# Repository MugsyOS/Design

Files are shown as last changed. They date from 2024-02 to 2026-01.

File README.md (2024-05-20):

# Design
All the parts! CAD, PCB and STL files for all of Mugsy's physical components. 

# Mech Control PCB
### Files:
* ****Schematic:**** mech-control-SCH-v0.2.fsch
* ****Board:**** mech-control-BRD-v0.2.fbrd
- - -

# Cone Mech
### Files:
* **Cone Pulley (2 files):** Print main and top.
* **Cone Support (1 file):** Print two for both left and right supports.
* **Stepper Motor Mount (1 file)**: Print one
* **Panels:** 
  * STLs provided for both top and bottom panels.
  * DXF files provided for those with access to a laser or CNC. We use 3mm cast acrylic which works out great. Other material can be used but must be 3mm. 
* **Idler Mount (1 File):** Print two.
- - -
### Additional Parts:
* **Stepper Motor**
  * Model:14HR05-0504S
  * Step Angle: 0.9deg
  * Single Unit Source: [STEPPERONLINE](https://www.omc-stepperonline.com/round-nema-14-bipolar-0-9deg-7ncm-9-91oz-in-0-5a-8-5v-36x12mm-4-wires-14hr05-0504s)
* **Signal** **Breakout PCB**: PCB files will be uploaded shortly. Single PCBs will also be available on the web store end of March 2024. 
* **Ethernet Socket:** RJ45 Connector, PCB Mount
* **M3 Threaded Inserts:**
  * Size: M3*4.6x5.7mm
* **M3 x 8mm Hex Head Machine Screws**
* **2GT Timing Pulley:** 
  * Type: 2M-AF
  * 20 Teeth
  * 6mm bore size
* **GT2 Toothless  Idler Pulleys (2x):** 3mm bore size
- - -
# Spout Mech
### Files:
* ****Spout Pulley Assembly (2 files):**** Print main and cap.
* ****Spout Pulley Assembly (2 files):**** Print main and cap.
* ****Spout Arm(1 file)****: Print one
- - -
### Additional Parts:
* ****Stepper Motor****
  * Model: 17HS08-1004S |
  * Step Angle: 1.8 deg
  * Single Unit Source: [STEPPERONLINE](https://www.omc-stepperonline.com/nema-17-bipolar-1-8deg-16ncm-22-6oz-in-1a-3-7v-42x42x20mm-4-wires-17hs08-1004s)
* ****M8 x 50mm Threaded Rod****
* ****8mm Shaft Lock Collar:**** 
  * 8mm(ID) * 14mm (OD) * 7mm (Depth)
* ****2GT Timing Pulley:****
  * 40 Teeth 
  * 8mm Bore Size
* ****GT2 Belt:**** 
  * 156mm * 6mm
- - -
# Screen Mount/Stabilizer
### Files:
* ****Screen Support:**** Left Side (single)
* ****Screen Support:**** Right Side (double)
* ****Screen Mount Main****: Print one
- - -
****All STEP/Fusion CAD source files will be uploaded as soon as possible.****

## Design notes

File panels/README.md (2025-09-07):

Vector files for all outer enclosure panels.

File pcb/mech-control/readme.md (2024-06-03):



**Components:**
* Nano Microcontroller
* 2x DRV8825 Stepper Drivers
* 2x10 pin headers for IO bridge
* 12v input
* 12v pass through
* 2x 47uf electrolytic capacitors
* 3x 100nf decoupling capacitors
* RJ45 Jack for connecting cone mech
* TRRS Jack for connecting spout

⠀**IO Bridge:** The IO bridge exposes all of the unused Nano’s pins except for reset and VIN:
* 2x 3V3
* 2x 5V
* 4x GND
* A0
* A1
* A2
* A4 / SDA
* A5 / SCL
* A6
* A7
* D0
* D1
* D12
* D13
* AREF

All of the analog pins can also be used as digital pins as needed.
**Board Files:** The schematic and board files have been uploaded to the design repo here.

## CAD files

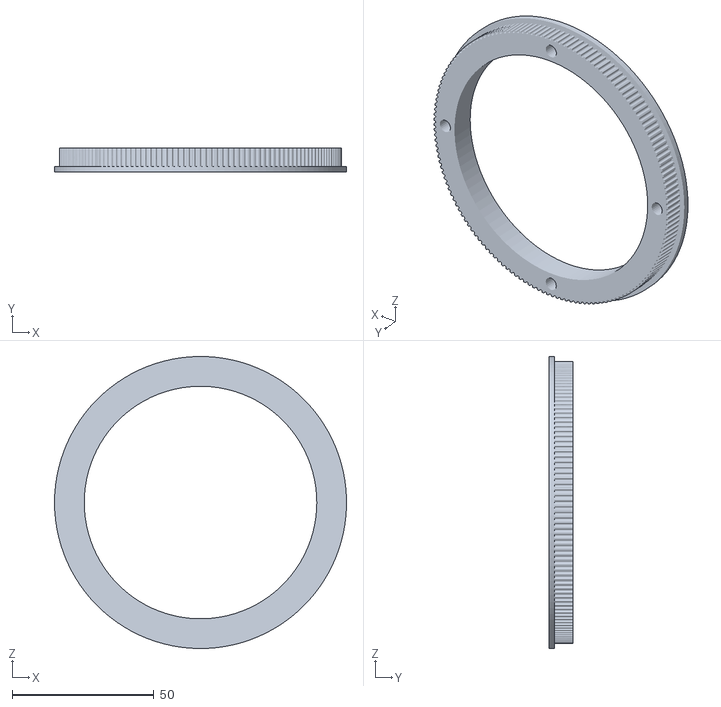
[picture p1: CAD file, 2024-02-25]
cone-mech/cone-pulley/cone-pulley-main-V1.stl
103.0 x 8.50 x 103.0

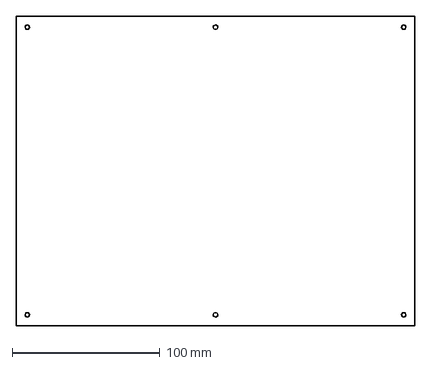
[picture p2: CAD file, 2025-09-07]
panels/head-unit-side-panel-main.dxf
270.0 x 210.0 mm

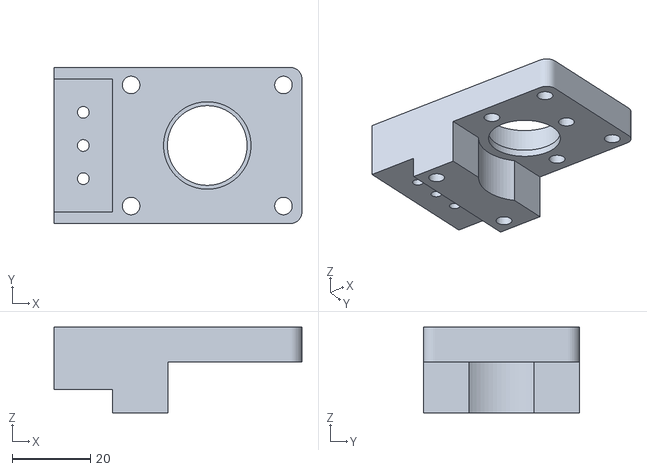
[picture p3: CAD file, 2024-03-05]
spout-mech/mugsy-spout-pulley-main-V0.8.stl
63.5 x 40.0 x 22.0

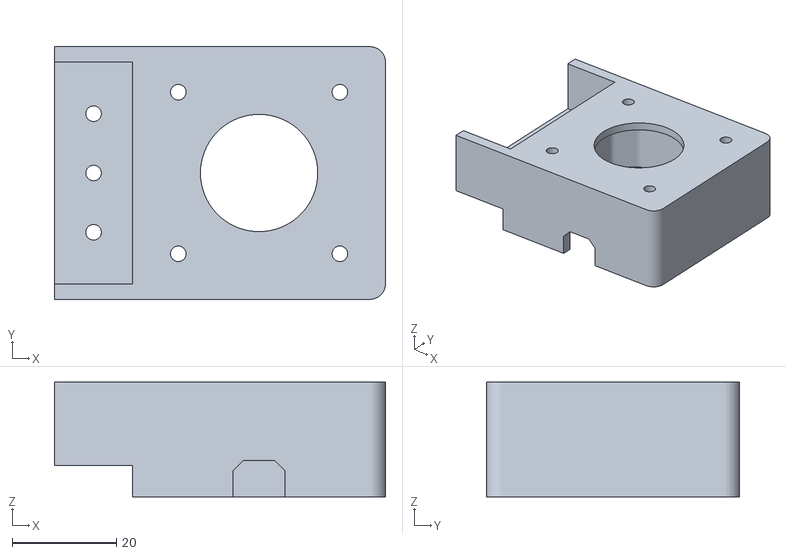
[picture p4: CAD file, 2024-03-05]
spout-mech/mugsy-spout-stepper-main-V0.8.stl
63.5 x 48.5 x 22.0

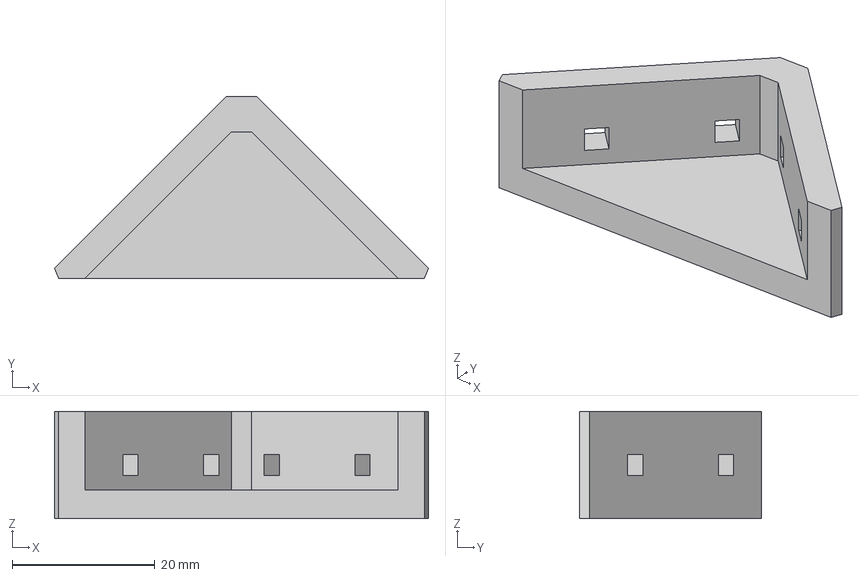
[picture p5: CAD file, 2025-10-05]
brackets/flipped-bracket.3mf
52.3 x 25.5 x 15.0 mm

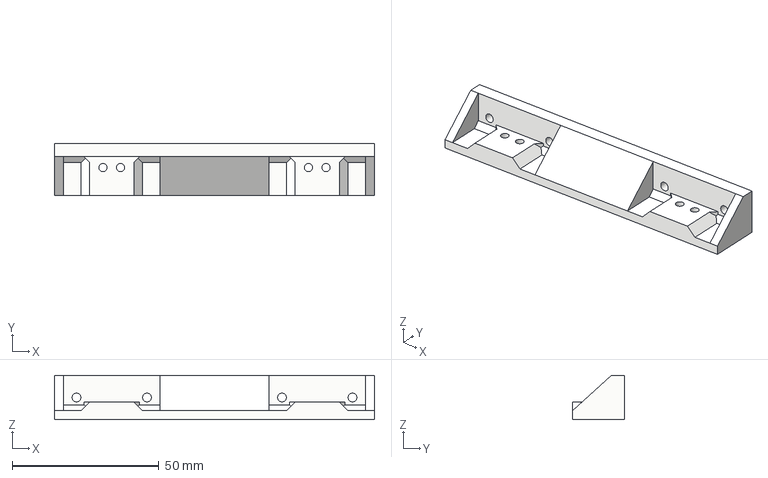
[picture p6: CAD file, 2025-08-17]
cone-mech-platform-scale/extended-mount-wip.3mf
109.0 x 17.7 x 15.0 mm

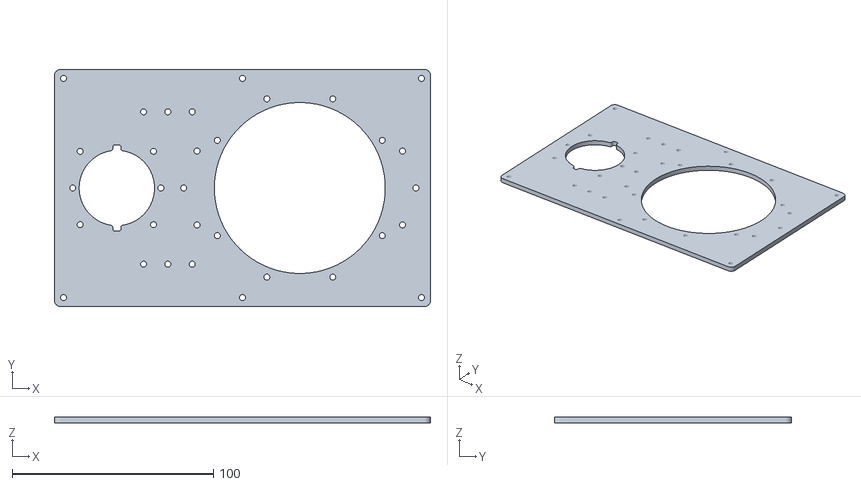
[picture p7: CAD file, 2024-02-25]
cone-mech/bottom-panel-V0.8.stl
187.0 x 118.0 x 3.00

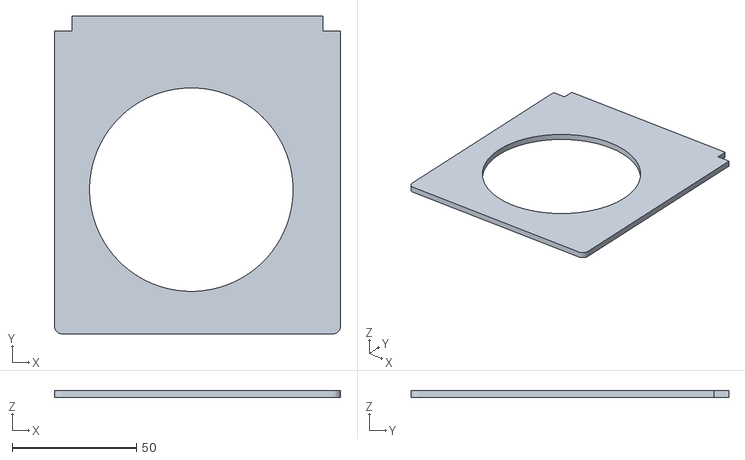
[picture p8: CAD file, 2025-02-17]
grinder/grinder-top-panel.stl
115.3 x 128.1 x 3.00

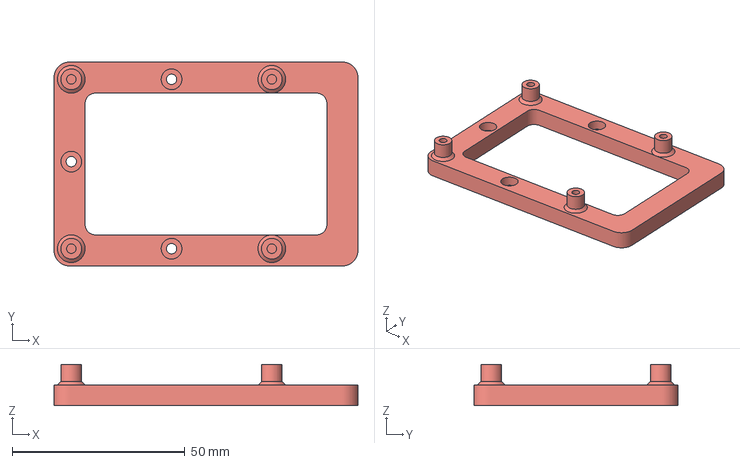
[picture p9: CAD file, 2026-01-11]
pcb/pi-pcb-mount-1 v1.3mf
87.9 x 59.0 x 12.0 mm

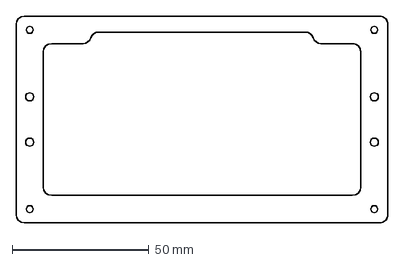
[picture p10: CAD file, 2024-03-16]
screen-mount/stabilizer-mount-V1.dxf
136.2 x 75.7 mm

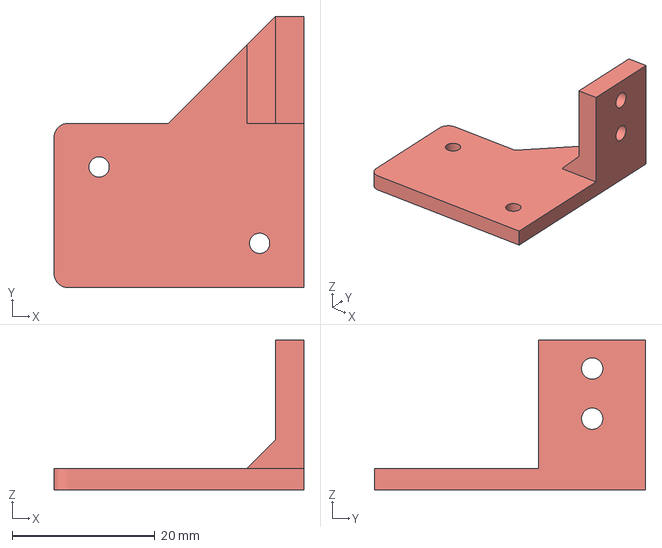
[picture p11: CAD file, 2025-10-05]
spout-mech/limit-mount-reversed.3mf
35.1 x 38.1 x 21.0 mm

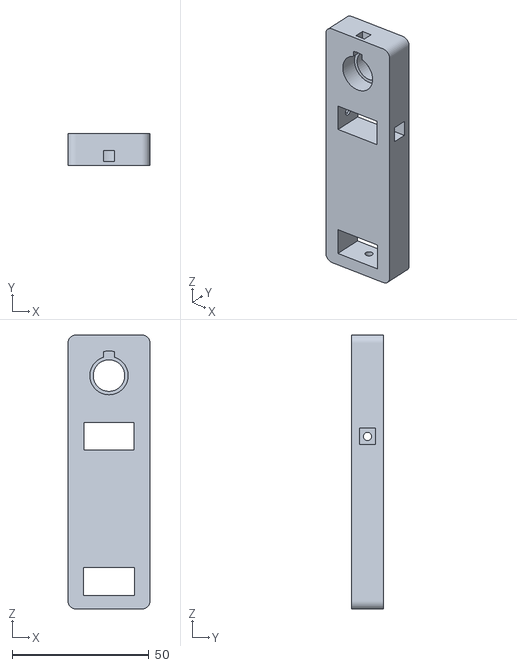
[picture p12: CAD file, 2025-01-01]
spout-mech/spout-v2/spout-arm.stl
30.0 x 11.8 x 100.0

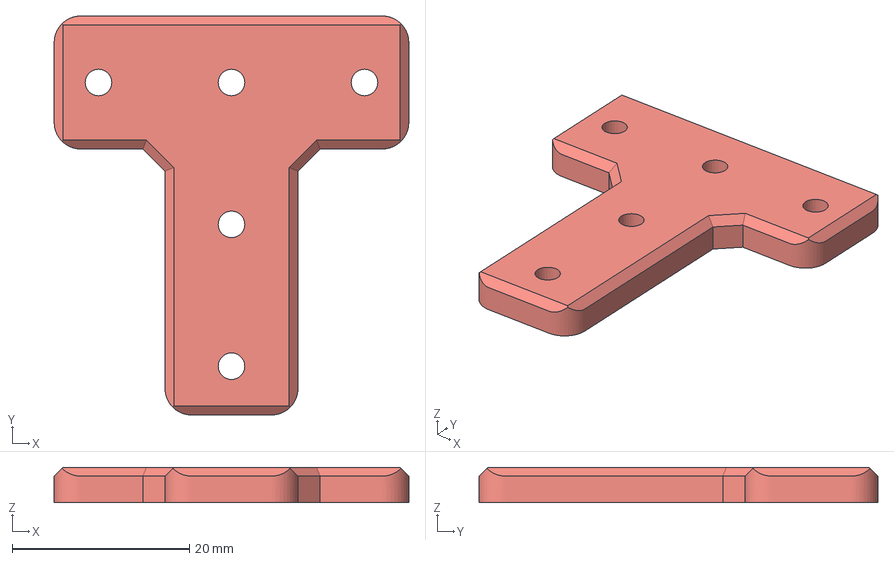
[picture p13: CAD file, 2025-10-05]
brackets/t-shape-bracket.3mf
40.0 x 45.0 x 4.00 mm

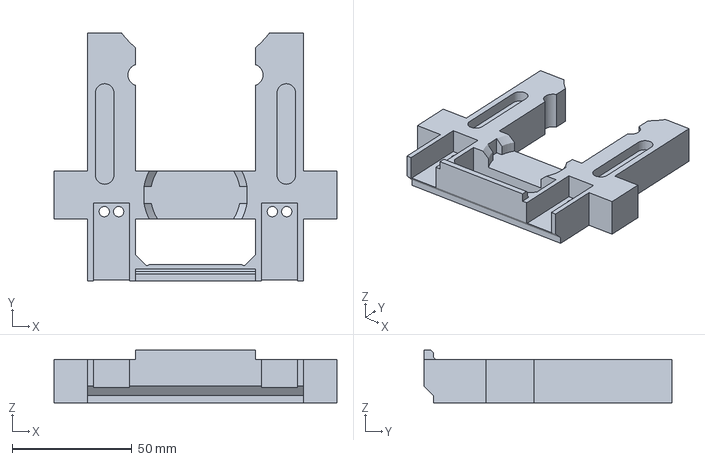
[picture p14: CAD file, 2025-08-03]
cone-mech-platform-scale/cone-mech-platform-scale.3mf
118.0 x 103.6 x 22.0 mm

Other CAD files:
spout-v2-1.1-with-cutout v2.3mf
cone-mech/cone-pulley/cone-pully-top-V1.stl
cone-mech/cone-support-V0.9.stl
grinder/grinder-face-panel.dxf
cone-mech/dxf/bottom-panel-V0.8.dxf
cone-mech/dxf/top-panel-V0.9.dxf
cone-mech/idler-mount-v0.7.stl
cone-mech/mid-section-V0.9.stl
cone-mech/stepper-motor-mount-V0.9.stl
cone-mech/top-panel-V0.9.stl
grinder/grinder-enclosure.3mf
grinder/grinder-enclosure.stl
panels/face-panel-primary-cut-file.dxf
panels/face-panel-secondary.dxf
pcb/primary-pcb-mount-plate.3mf
screen-mount/screen-support-double-V1.dxf
screen-mount/screen-support-single-V1.dxf
spout-mech/limit-switch-mount.stl
spout-mech/mugsy-spout-V0.4.stl
spout-mech/mugsy-spout-pulley-cap-V0.8.stl
spout-mech/mugsy-spout-stepper-cap-V0.8.stl
spout-mech/spout-v2/spout-mount.stl
spout-mech/spout-v2/tube-mount.stl

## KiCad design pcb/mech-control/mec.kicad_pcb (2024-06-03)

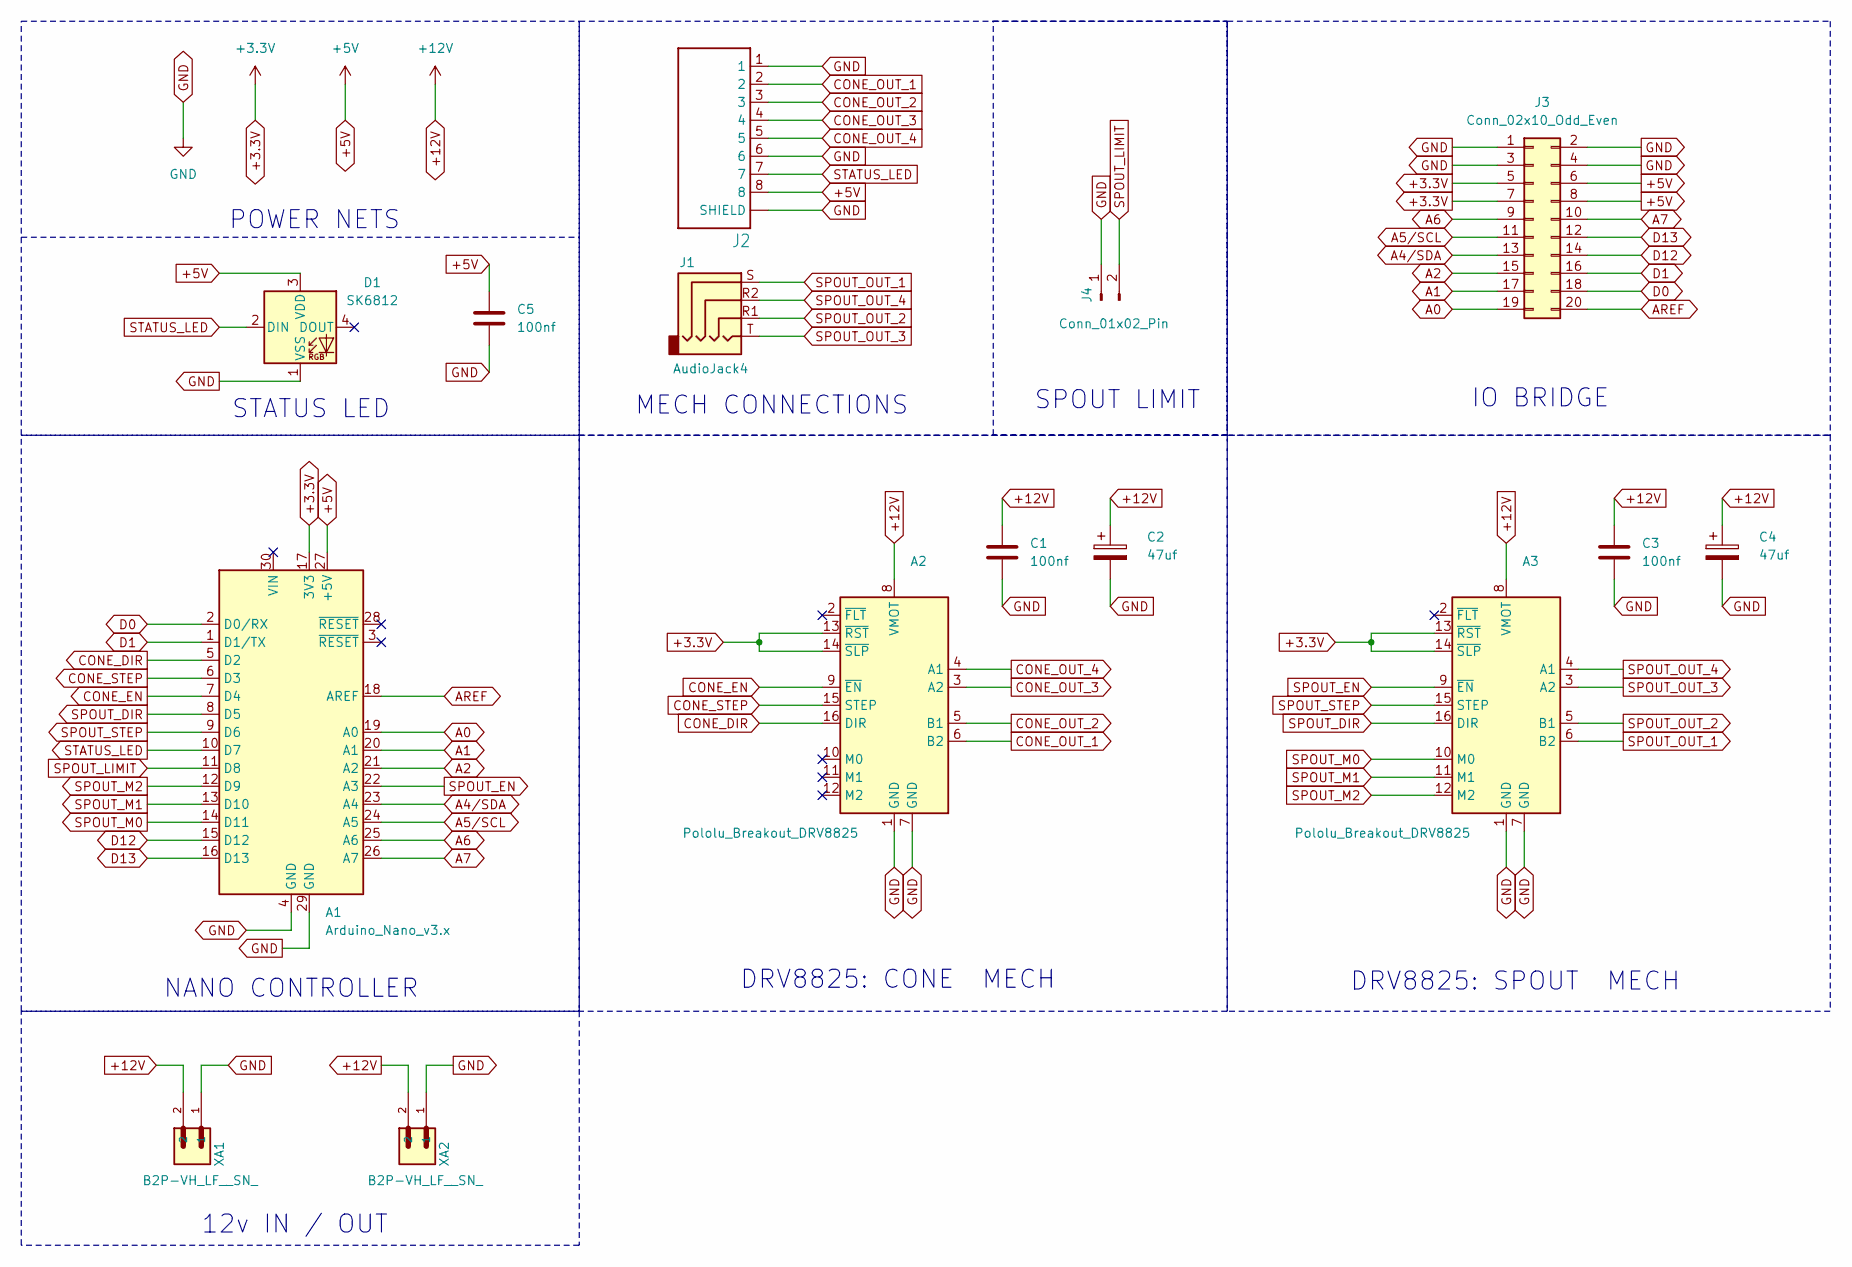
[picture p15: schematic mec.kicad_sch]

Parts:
A1: Arduino_Nano_v3.x; Arduino_Nano
A2, A3: Pololu_Breakout_DRV8825; Pololu_Breakout-16_15.2x20.3mm
C1, C3, C5: 100nf; C_0805_2012Metric
C2, C4: 47uf; CP_Elec_6.3x7.7
D1: SK6812; LED_SK6812_PLCC4_5.0x5.0mm_P3.2mm
J1: AudioJack4; Jack_3.5mm_KoreanHropartsElec_PJ-320D-4A_Horizontal
J2: MUGSY_RJ45-8N-B
J3: Conn_02x10_Odd_Even; PinHeader_2x10_P2.54mm_Vertical
J4: Conn_01x02_Pin; JST_XH_B2B-XH-A_1x02_P2.50mm_Vertical
XA1, XA2: B2P-VH_LF__SN_; JST_B2P-VH_LF__SN_

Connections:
+3.3V: A1.17 (3V3), A2.13 (~RST), A2.14 (~SLP), A3.13 (~RST), A3.14 (~SLP), J3.5, J3.7
+5V: A1.27 (+5V), C5.1, D1.3 (VDD), J2.8, J3.6, J3.8
+12V: A2.8 (VMOT), A3.8 (VMOT), C1.1, C2.1, C3.1, C4.1, XA1.2, XA2.2
A0: A1.19 (A0), J3.19
A1: A1.20 (A1), J3.17
A2: A1.21 (A2), J3.15
A4/SDA: A1.23 (A4), J3.13
A5/SCL: A1.24 (A5), J3.11
A6: A1.25 (A6), J3.9
A7: A1.26 (A7), J3.10
AREF: A1.18 (AREF), J3.20
CONE_DIR: A1.5 (D2), A2.16 (DIR)
CONE_EN: A1.7 (D4), A2.9 (~EN)
CONE_OUT_1: A2.6 (B2), J2.2
CONE_OUT_2: A2.5 (B1), J2.3
CONE_OUT_3: A2.3 (A2), J2.4
CONE_OUT_4: A2.4 (A1), J2.5
CONE_STEP: A1.6 (D3), A2.15 (STEP)
D0: A1.2 (D0/RX), J3.18
D1: A1.1 (D1/TX), J3.16
D12: A1.15 (D12), J3.14
D13: A1.16 (D13), J3.12
GND: A1.4 (GND), A1.29 (GND), A2.1 (GND), A2.7 (GND), A3.1 (GND), A3.7 (GND), C1.2, C2.2, C3.2, C4.2, C5.2, D1.1 (VSS), J2.1, J2.6, J2.9 (SHIELD), J2.10 (SHIELD), J3.1, J3.2, J3.3, J3.4, J4.1, XA1.1, XA2.1
SPOUT_DIR: A1.8 (D5), A3.16 (DIR)
SPOUT_EN: A1.22 (A3), A3.9 (~EN)
SPOUT_LIMIT: A1.11 (D8), J4.2
SPOUT_M0: A1.14 (D11), A3.10 (M0)
SPOUT_M1: A1.13 (D10), A3.11 (M1)
SPOUT_M2: A1.12 (D9), A3.12 (M2)
SPOUT_OUT_1: A3.6 (B2), J1.S
SPOUT_OUT_2: A3.5 (B1), J1.R1
SPOUT_OUT_3: A3.3 (A2), J1.T
SPOUT_OUT_4: A3.4 (A1), J1.R2
SPOUT_STEP: A1.9 (D6), A3.15 (STEP)
STATUS_LED: A1.10 (D7), D1.2 (DIN), J2.7

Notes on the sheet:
12v IN / OUT
SPOUT LIMIT
MECH CONNECTIONS
POWER NETS
NANO CONTROLLER
IO BRIDGE
STATUS LED
DRV8825: SPOUT MECH
DRV8825: CONE MECH

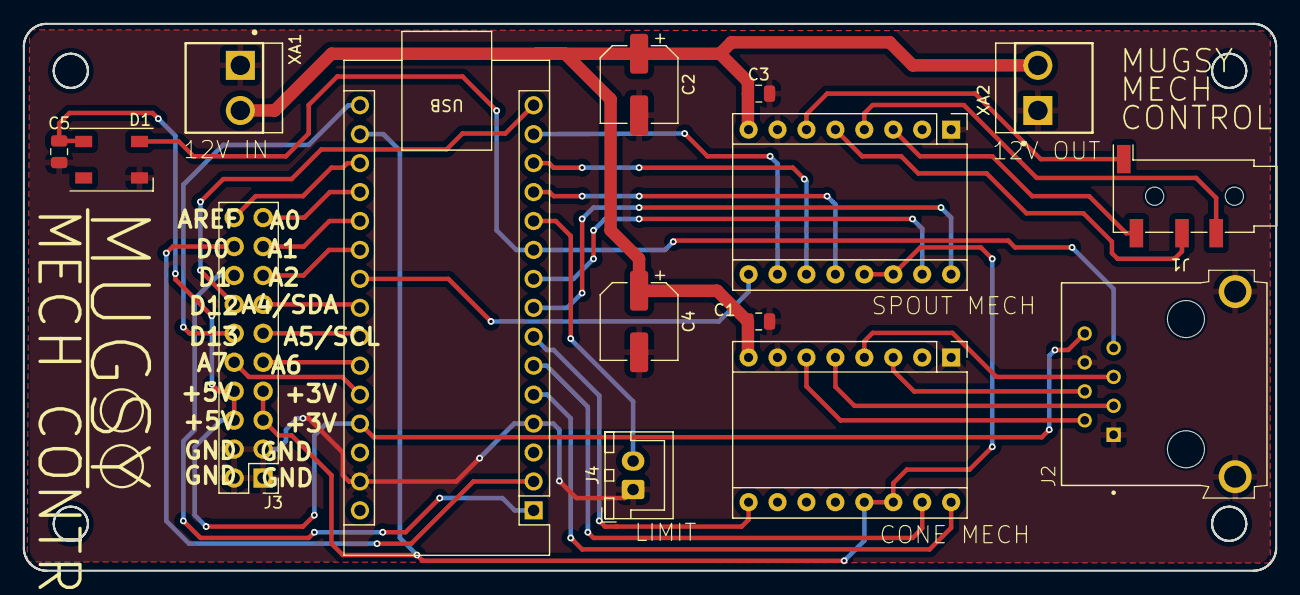
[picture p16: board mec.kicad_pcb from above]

Board: 2 copper layers, 109.9 x 48.0 mm, 15 parts (0 on the bottom side), 35 nets.

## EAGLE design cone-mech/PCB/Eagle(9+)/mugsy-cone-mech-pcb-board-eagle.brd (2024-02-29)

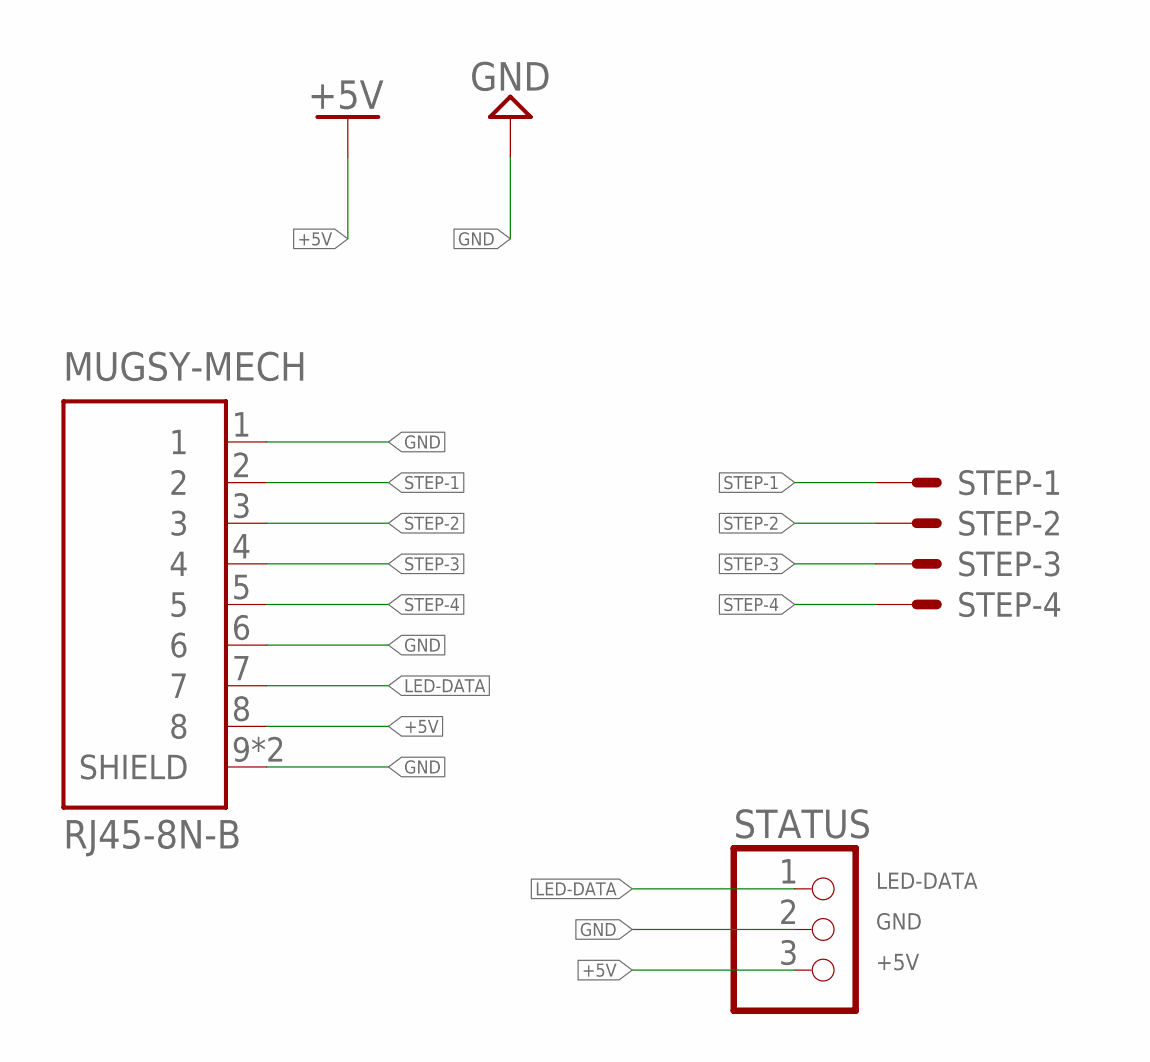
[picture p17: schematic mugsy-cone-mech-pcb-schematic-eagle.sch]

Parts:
MUGSY-MECH: RJ45-8N-B; TE_RJ45-8N-B
STATUS: PINHD-1X3CB; 1X03-CLEANBIG
STEP: JST-XH-04-PIN-ROUND-PAD; JST-XH-04-PACKAGE-ROUND-PAD

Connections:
+5V: MUGSY-MECH.8, STATUS.3
GND: MUGSY-MECH.1, MUGSY-MECH.6, MUGSY-MECH.9 (SHIELD), MUGSY-MECH.10 (SHIELD), STATUS.2
LED-DATA: MUGSY-MECH.7, STATUS.1
STEP-1: MUGSY-MECH.2, STEP.1
STEP-2: MUGSY-MECH.3, STEP.2
STEP-3: MUGSY-MECH.4, STEP.3
STEP-4: MUGSY-MECH.5, STEP.4

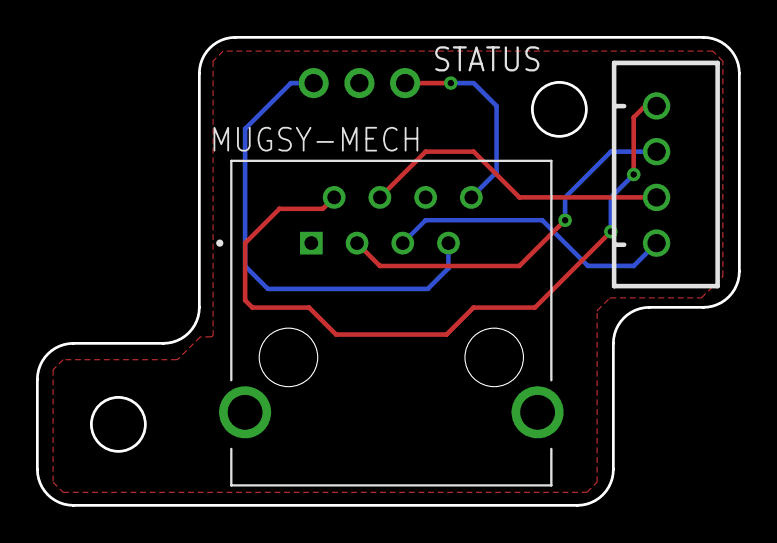
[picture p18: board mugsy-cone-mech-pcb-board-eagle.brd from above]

Board: 2 copper layers, 39.0 x 26.0 mm, 3 parts (0 on the bottom side), 7 nets.

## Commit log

2024-02-29 add mugsy cone mech PCB board and schematic for fusion and eagle
    [mugsy-cone-mech-pcb-board-eagle.brd, mugsy-cone-mech-pcb-schematic-eagle.sch]
2024-06-03 Add kicad schematic and board for Mech Control PCB
    [mec.kicad_pcb, mec.kicad_sch]
2024-07-22 Add spout limit switch
    [limit-switch-mount.stl]
2025-01-01 add spout-v2 stl files
    With the pump switch, the spout has been redesigned to handle the single tube with larger diameter
    [spout-arm.stl, spout-mount.stl, tube-mount.stl]
2025-02-17 add grinder enclosure design files
    [grinder-enclosure.stl, grinder-top-panel.stl]
2025-08-17 Add files via upload
    Add updated enclosure side cone mech tray mount.
    [extended-mount-wip.3mf]
2025-09-07 Add README for outer enclosure panels
2025-10-05 Add limit switch mount for new switch position
    [limit-mount-reversed.3mf]
2026-01-11 add pi pcb mount
    [pi-pcb-mount-1 v1.3mf]
